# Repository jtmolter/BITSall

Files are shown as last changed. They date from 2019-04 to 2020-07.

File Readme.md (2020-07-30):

# Balloon Iridium Telemetry System

## DEPRECATED
Now part of https://github.com/UMDBPP/command_module

## Overview
This payload functions with an Iridium 9603 on a RockBlock carrier board. BITS has flown in various forms starting with NS-75 and continuously since NS-79 (10+ at this point) Iridium communications provide tracking from launch to landing, allowing for retrival of exact coordinates when landing in an area with no cell coverage. Additionally, the payload has been used as a long range link to then send data via XBee to other payloads.

Documentation is currently WIP (but for real this time)

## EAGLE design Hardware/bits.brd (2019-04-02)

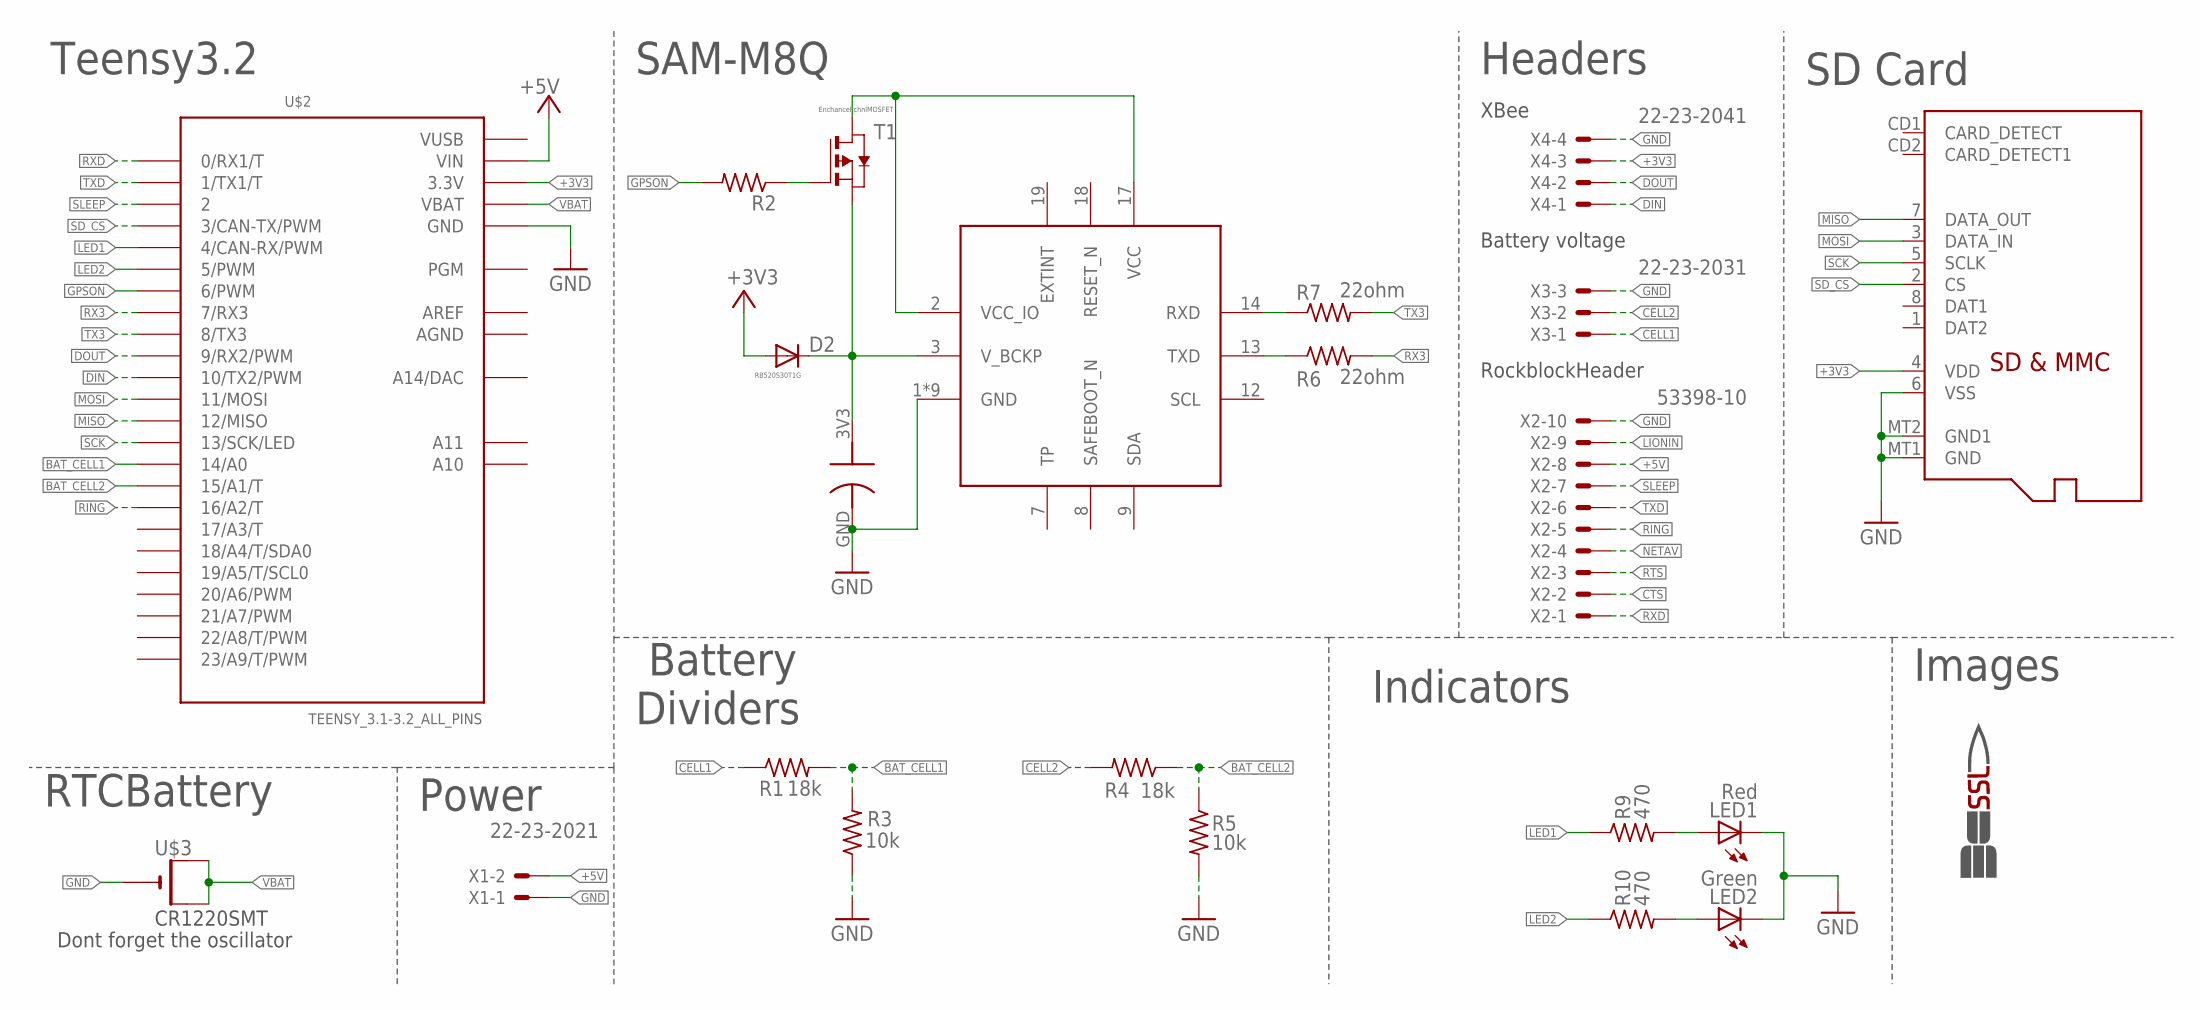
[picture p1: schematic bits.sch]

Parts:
C1: 0.2F elna supercap; ELNASUPERCAP
D2: RB520S30T1G; SOD523
IC1: SAM-M8Q
IMAG1: SSL.3IN_SILK; SSL_SILK_.3IN
LED1: Red; CHIP-LED0603
LED2: Green; CHIP-LED0603
R1, R4: 18k; R0603
R2: R-US_R0603; R0603
R3, R5: 10k; R0603
R6, R7: 22ohm; R0603
R9, R10: 470; R0603
T1: EnchancePchnlMOSFET; SOT-23
U$1: MICROSD
U$2: TEENSY_3.1-3.2_ALL_PINS; TEENSY_3.0-3.2&LC_ALL_PINS
U$3: CR1220SMT; CR1220-SMD
X1: 22-23-2021
X2: 53398-10
X3: 22-23-2031
X4: 22-23-2041

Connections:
+3V3: D2.A, U$1.4 (VDD), U$2.3.3V, U$2.3.3V1 (3.3V), X4.3
+5V: U$2.VIN, X1.2, X2.8
AGND: U$2.AGND
AREF: U$2.AREF
BAT_CELL1: R1.2, R3.2, U$2.14/A0
BAT_CELL2: R4.1, R5.1, U$2.15/A1 (15/A1/T)
CELL1: R1.1, X3.1
CELL2: R4.2, X3.2
CTS: X2.2
DIN: U$2.10 (10/TX2/PWM), X4.1
DOUT: U$2.9 (9/RX2/PWM), X4.2
GND: C1.GND, IC1.1 (GND), IC1.4 (GND), IC1.5 (GND), IC1.6 (GND), IC1.10 (GND), IC1.11 (GND), IC1.15 (GND), IC1.16 (GND), IC1.20 (GND), LED1.C, LED2.C, R3.1, R5.2, U$1.6 (VSS), U$1.MT1 (GND), U$1.MT2 (GND1), U$2.GND, U$2.GND1 (GND), U$3.-, X1.1, X2.10, X3.3, X4.4
GPS3V3: C1.3V3, D2.C, IC1.3 (V_BCKP), T1.2 (S)
GPSON: R2.2, U$2.6 (6/PWM)
LED1: R9.1, U$2.4 (4/CAN-RX/PWM)
LED2: R10.1, U$2.5 (5/PWM)
LIONIN: X2.9
MISO: U$1.7 (DATA_OUT), U$2.12 (12/MISO)
MOSI: U$1.3 (DATA_IN), U$2.11 (11/MOSI)
unnamed: R2.1, T1.3 (G)
unnamed: LED2.A, R10.2
unnamed: LED1.A, R9.2
unnamed: IC1.14 (RXD), R7.1
unnamed: IC1.13 (TXD), R6.1
unnamed: IC1.2 (VCC_IO), IC1.17 (VCC), T1.1 (D)
NETAV: X2.4
RING: U$2.16/A2 (16/A2/T), X2.5
RTS: X2.3
RX3: R6.2, U$2.7 (7/RX3)
RXD: U$2.0 (0/RX1/T), X2.1
SCK: U$1.5 (SCLK), U$2.13 (13/SCK/LED)
SD_CS: U$1.2 (CS), U$2.3 (3/CAN-TX/PWM)
SLEEP: U$2.2, X2.7
TX3: R7.2, U$2.8 (8/TX3)
TXD: U$2.1 (1/TX1/T), X2.6
VBAT: U$2.VBAT, U$3.+$1 (+), U$3.+$2 (+1)
VUSB: U$2.VUSB

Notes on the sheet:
SAM-M8Q
Teensy3.2
Headers
SD Card
RTCBattery
Dont forget the oscillator
RockblockHeader
Battery Dividers
Indicators
Power
Battery voltage
XBee
Images

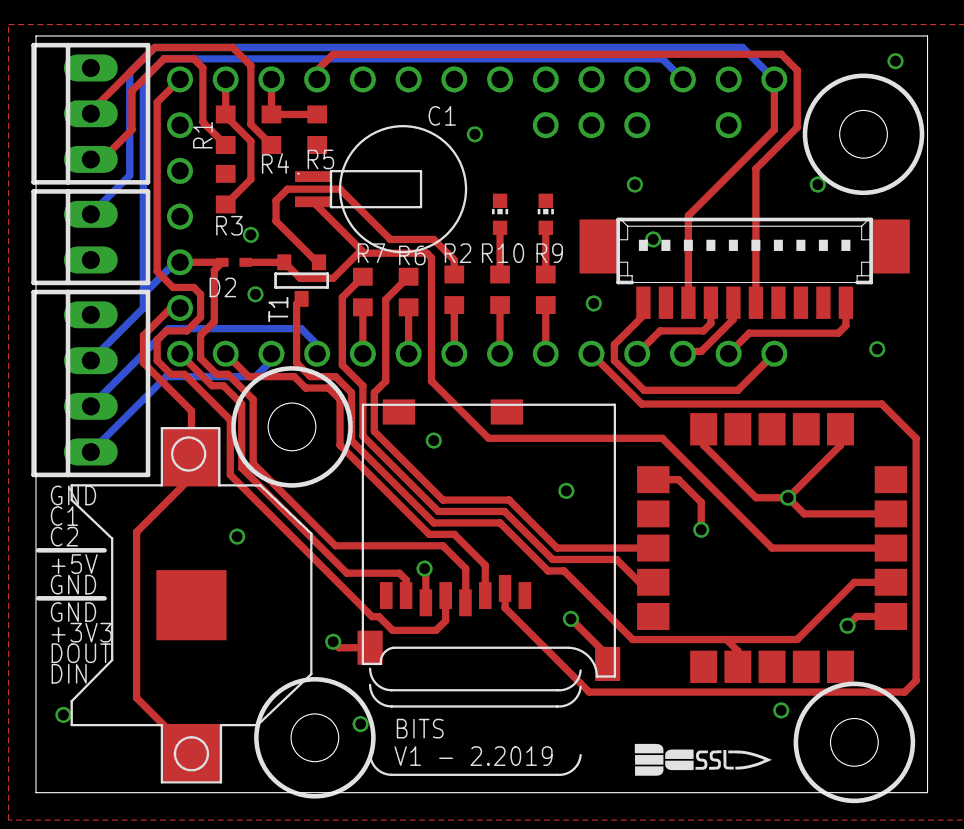
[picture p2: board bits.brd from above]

Board: 2 copper layers, 49.5 x 42.0 mm, 23 parts (1 on the bottom side), 30 nets.

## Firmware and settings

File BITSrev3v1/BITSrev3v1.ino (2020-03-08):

//UMD Nearspace Iridium Tracking Payload (BITS) {Balloon Iridium Tracking System)
//Written by Jonathan Molter and Luke Renegar
//Uses an Iridium 9603 SBD Modem for effective unlimited range, without the need for our own RF blackmagics*
//This software is specifically written with the bits3 board revisision

#include <XBee.h> //If using 900HP's this must be the custom cpp (or really any post gen2 XBees)
#include <IridiumSBD.h>
#include <SD.h>
#include <TinyGPS.h>

//Serial Ports (sketch requires 4 {Wellll technically 3 + DEBUG})
#define OutputSerial Serial     //USB debug
#define IridiumSerial Serial1   //Iridium 9603
#define XBeeSerial Serial2      //XBee
#define gpsserial Serial3       //GPS
//Pins
#define SLEEP_PIN_NO 5    // Iridium Sleep Pin
#define RING_PIN_NO 23    // Iridium Ring Alert Pin
#define chipSelect 6      // Pin for SPI
#define greenLED 2        // Green Status LED
#define redLED 3          // Red Status LED
#define GPS_ON 4

#define DIAGNOSTICS false // Change this to see diagnostics
#define XBEE_DEBUG true
const bool USEGPS = true; // Should be true 99% of the time
bool sendingMessages = true; // Whether or not the device is sending messages; begins as true TODO

//Setting default datarates
#define GPS_BAUD 9600
#define SBD_BAUD 19200

//XBee Addresses
const uint32_t BitsSL = 0x417B4A3B;   //BITS (white)Specific to the XBee on Bits (the Serial Low address value)
const uint32_t GroundSL = 0x417B4A36; //GroundStations (u.fl)
const uint32_t BlueSL = 0x417B4A3A;   //Blue (Blue Tape)
const uint32_t WireSL = 0x419091AC;   //Wire (wire antenna)
const uint32_t UniSH = 0x0013A200;    //Common across any and all XBees

//XBee object / global variables
XBee xbee = XBee();
XBeeResponse response = XBeeResponse();
ZBTxStatusResponse txStatus = ZBTxStatusResponse();
ZBRxResponse rx = ZBRxResponse();
ModemStatusResponse msr = ModemStatusResponse();
const int xbeeRecBufSize = 49; //Rec must be ~15bytes larger than send
const int xbeeSendBufSize = 34;
uint8_t xbeeRecBuf[xbeeRecBufSize];
uint8_t xbeeSendBuf[xbeeSendBufSize];

//GPS data struct and object
struct GPSdata{
  float GPSLat=-1;
  float GPSLon=-1;
  unsigned long GPSTime=-1;
  long GPSAlt=-1;
  int GPSSats=-1;
};
TinyGPS gps;
GPSdata gpsInfo;

//Interval definitions
const long signalCheckInterval = 15000;
unsigned long messageTimeInterval = 60000; // In milliseconds; 300000 is 5 minutes; defines how frequently the program sends messages, now changeable                                                                      
const long shutdownTimeInterval = 14400000; // In milliseconds; 14400000 is 4 hours; defines after what period of time the program stops sending messages

//Initializing Log Files; Must be in form XXXXXXXX.log; no more than 8 'X' characters
File gpsLogFile;
File rxLogFile;
File txLogFile;

const String gpsLogName =   "GPS.LOG";  //1 sec position/altitude updates
const String eventLogName = "EVENT.LOG";//Events Iridium/XBee (Special one thanks to Luke)
const String rxLogName =    "RX.LOG";   //Iridium Uplinks   (toBalloon)
const String txLogName =    "TX.LOG";   //Iridium Downlinks (toGround)



// Program Timing
unsigned long startTime;
unsigned long lastMillisOfMessage = 0;
unsigned long lastSignalCheck = 0;
unsigned long lastLog = 0;

// Iridium Global Buffers
//#define SBD_RX_BUFFER_SIZE 100 // Max size of an SBD message TODO(1) DELETE
#define maxPacketSize 128		//Standard(GPS/TIME, etc.) + Message Data
#define downlinkMessageSize 100 //Message Data
#define RX_BUF_LENGTH 49		//Uplink Buffer Size

uint8_t rxBuf[RX_BUF_LENGTH]; 			   //Uplink Buffer
//uint8_t sbd_rx_buf[SBD_RX_BUFFER_SIZE];  //TODO(1) DELETE ?(what is this even doing...)
char downlinkMessage2[downlinkMessageSize];//Downlink Buffer
bool downlinkData;

int sbd_csq; //Signal Qual

// The best global
int arm_status = 42;//armed when = 42

// Declare the IridiumSBD object
IridiumSBD modem(IridiumSerial);

//Possible Iridium Error Codes
#define ISBD_SUCCESS             0
#define ISBD_ALREADY_AWAKE       1
#define ISBD_SERIAL_FAILURE      2
#define ISBD_PROTOCOL_ERROR      3
#define ISBD_CANCELLED           4
#define ISBD_NO_MODEM_DETECTED   5
#define ISBD_SBDIX_FATAL_ERROR   6
#define ISBD_SENDRECEIVE_TIMEOUT 7
#define ISBD_RX_OVERFLOW         8
#define ISBD_REENTRANT           9
#define ISBD_IS_ASLEEP           10
#define ISBD_NO_SLEEP_PIN        11
#define SBD

void setup()
{
  Serial.begin(9600);
  delay(5);
  Serial.println("BITSrev3v1");
  gpsserial.begin(9600);
  GPSINIT(); //Setup the GPS
  gpsserial.end();
  gpsserial.begin(GPS_BAUD);
  IridiumSerial.begin(SBD_BAUD);
  Serial2.begin(9600);
  xbee.setSerial(Serial2);
  startBlinks();

//Open Files
  SD.begin(chipSelect);
  gpsLogFile = SD.open(gpsLogName, FILE_WRITE);
  rxLogFile = SD.open(rxLogName, FILE_WRITE);
  txLogFile = SD.open(txLogName, FILE_WRITE);
  delay(10);
  gpsLogFile.println("INIT_GPS_LOG");
  rxLogFile.println("INIT_RX_LOG");
  txLogFile.println("INIT_TX_LOG");
  gpsLogFile.flush();
  rxLogFile.flush();
  txLogFile.flush();
  Serial.println("MadeLogs");
  logprintln("INIT_LOG_LOG");

  //memset(sbd_rx_buf, 0, SBD_RX_BUFFER_SIZE); //TODO(1) DELETE ?

  //XBee Init Message to ground stations
  String("Init").getBytes(xbeeSendBuf,xbeeSendBufSize);   //Convert "Init" 2 bytes, dump into Message buffer
  xbeeSend(GroundSL,xbeeSendBuf);                         //(Target,Message)
  
int err;
#ifdef SBD  // Begin satellite modem operation
  OutputSerial.println("Starting modem...");
  err = modem.begin();
  modem.useMSSTMWorkaround(false);//SUPER NF TESTTHIS TODO(2)
  modem.adjustSendReceiveTimeout(120);
  if (err != ISBD_SUCCESS)
  {
    OutputSerial.print("Begin failed: error ");
    OutputSerial.println(err);
    logprint("Begin failed: error ");
    logprintln(err);
    if ((err == ISBD_NO_MODEM_DETECTED) || (err == 5))
      Serial.println("No modem detected: check wiring.");
    return;
  }
  OutputSerial.println("Modem started");

  #ifdef ISBD_CHECK_FIRMWARE // Example: Print the firmware revision
    char version[12];
    err = modem.getFirmwareVersion(version, sizeof(version));
    if (err != ISBD_SUCCESS)
    {
      OutputSerial.print("FirmwareVersion failed: error ");
      OutputSerial.println(err);
      logprint("FirmwareVersion failed: error ");
      logprintln(err);
      return;
    }
    OutputSerial.print("Firmware Version is ");
    OutputSerial.println(version);
  #endif

  // From 0-5, 2 or better is preferred (Still works at 0)
  err = modem.getSignalQuality(sbd_csq);
  if (err != ISBD_SUCCESS)
  {
    OutputSerial.print("SignalQuality failed: error ");
    OutputSerial.println(err);
    logprint("SignalQuality failed: error ");
    logprintln(err);
    sbd_csq = -1;
    return;
  }

  OutputSerial.print("From 0 to 5, signal qual is: ");
  OutputSerial.println(sbd_csq);
#endif

String gpsPacket;

if(USEGPS){
  OutputSerial.println("TryingGPS");

  //GPS LOCK INIT
    while((gpsInfo.GPSAlt<=0)||(gpsInfo.GPSAlt>100000)) //Outside of a reasonable range
    {
      //delay(500);
      //output();
      while (gpsserial.available()){
          if (gps.encode(gpsserial.read())){
          gpsInfo = getGPS();
        break;
        }
      }
    }
    
    gpsPacket = String(gpsInfo.GPSTime)+","+String(gpsInfo.GPSLat,4)+","+String(gpsInfo.GPSLon,4)+","+String(gpsInfo.GPSAlt);
    txLogFile.println(gpsPacket);
    logprintln("GotLock");
    gpsLockBlink();
    OutputSerial.println("gpsPacket  " +String(gpsPacket));
}else{
  OutputSerial.println("Not Using GPS");
  gpsPacket = "test";
}


//Honestly consider canning this whole section, really not needed considering loop does the same thing
#ifdef SBD
// Send the message
  char sbd_buf[49];//TX BUFFER
  OutputSerial.print("Trying to send the message.  This might take several minutes.\r\n");
  gpsPacket.toCharArray(sbd_buf,49);
  err = modem.sendSBDText(sbd_buf);//Sends an initial packet AFTER gps has locked.
  if (err != ISBD_SUCCESS)
  {
    OutputSerial.println("sendSBDText failed: error "+String(err));
    OutputSerial.println();
    logprint("sendSBDText failed: error ");
    logprintln(err);
    if (err == ISBD_SENDRECEIVE_TIMEOUT)
      OutputSerial.println("Try again with a better view of the sky.");
      logprintln("Try again with a better view of the sky.");
  }else{
    OutputSerial.println("Success, sent = "+String(sbd_buf));
    logprintln("Success, sent = "+String(sbd_buf));
  }
#endif

        String("EnteringLoop").getBytes(xbeeSendBuf,xbeeSendBufSize);
        xbeeSend(GroundSL,xbeeSendBuf);
}

void loop()
{  
  ISBDCallback(); //During the Iridium retry protocol anything that still needs to happen needs to go in here

  xbeeRead();
  LogPacket();
  
//Check Signal Quality
  if (((millis() - lastSignalCheck) > signalCheckInterval) && (millis() < shutdownTimeInterval)) {
    int new_csq = 0;
    int csq_err = modem.getSignalQuality(new_csq);
    if(csq_err == 0) // if executed during an Iridium session, this will yield an ISBD_REENTRANT; keep previous value
    {
      sbd_csq = new_csq;
    }
    else if(csq_err == ISBD_REENTRANT){
      //KeepCalm, carry on  
    }else{
      logprint("CSQ error code = ");
      logprintln(csq_err);
    }
    lastSignalCheck = millis();
  }

//Transmit Via Iridium
  // If not currently transmitting, and at time, and transmitting messages ON, transmit
  if ((sbd_csq > 0 && (millis() - lastMillisOfMessage) > messageTimeInterval) && (millis() < shutdownTimeInterval) && sendingMessages) {

    size_t rx_buf_size = RX_BUF_LENGTH; //RECENT CHANGE via TODO(1)

  //Assesmble the packet to be sent to the ground
    char Packet2[maxPacketSize];
    snprintf(Packet2,maxPacketSize,"%06d,%4.4f,%4.4f,%u",gpsInfo.GPSTime,gpsInfo.GPSLat,gpsInfo.GPSLon,gpsInfo.GPSAlt); //Build the packet

  //If there is stuff to downlink than do
    if(downlinkData){ 
      logprint("DownAttempt: ");
      logprintln(downlinkMessage2);
      strncat(Packet2,downlinkMessage2,(maxPacketSize - strlen(Packet2) - 1));  //Add data from downlinkMessage2 into Packet2, check for size
      downlinkData = false;
      memset(downlinkMessage2, 0, downlinkMessageSize);                         //Clear downlink message
    }    
    
    logprint(Packet2);logprintln("Loop Sending");
    OutputSerial.println("Loop Sending");
    txLogFile.println(Packet2);
    txLogFile.flush();

  //SEND/RECEIVE DATA, return status
    uint8_t sbd_err = modem.sendReceiveSBDText(Packet2,rxBuf,rx_buf_size);  //Message, RecieveBuffer, SizeOfBuffer

    logprint("SBD send receive completed with return code: ");
    logprintln(sbd_err); // 0 is good
    OutputSerial.println("Send Error:  " +String(sbd_err));

    rxLogFile.print(String(gpsInfo.GPSTime)); //Log time of RX
    rxLogFile.print("\t");
    
  //Process Received Messages
    uplink(); //Run uplink message handling (bitsIncoming)
 
    for (int k = 0; k < rx_buf_size; k++)//Prints RX characters to SD file
    {
      rxLogFile.write(rxBuf[k]); //Trying write instead of print, shoud fix garbage data
      rxBuf[k] = 0;
      delay(1);
    }
    rxLogFile.println();
    rxLogFile.flush();

    lastMillisOfMessage = millis();
  }
}//End of Loop


bool ISBDCallback() //Functions that occurs during packet transmit sequence delay
{
  //Parse the GPS without delay
  while (gpsserial.available()){
    if (gps.encode(gpsserial.read())){
      gpsInfo = getGPS();
      break;
    }
  }

  //Check the Xbee
  xbeeRead();
  
  LogPacket();
  
  return true;
}

static void logprint(String s)
{
  File dataFile = SD.open(eventLogName, FILE_WRITE);
  dataFile.print(s);
  dataFile.close();
}

static void logprint(int i)
{
  File dataFile = SD.open(eventLogName, FILE_WRITE);
  dataFile.print(i);
  dataFile.close();
}

static void logprint(double d)
{
  File dataFile = SD.open(eventLogName, FILE_WRITE);
  dataFile.print(d);
  dataFile.close();
}

static void logprintln(String s)
{
  File dataFile = SD.open(eventLogName, FILE_WRITE);
  dataFile.println(s);
  dataFile.close();
}

static void logprintln(int i)
{
  File dataFile = SD.open(eventLogName, FILE_WRITE);
  dataFile.println(i);
  dataFile.close();
}

static void logprintln(double d)
{
  File dataFile = SD.open(eventLogName, FILE_WRITE);
  dataFile.println(d);
  dataFile.close();
}

static void logprintln32(uint32_t d)
{
  File dataFile = SD.open(eventLogName, FILE_WRITE);
  dataFile.println(d,HEX);
  dataFile.close();
}

#if DIAGNOSTICS
void ISBDConsoleCallback(IridiumSBD *device, char c)
{
  OutputSerial.write(c);
}

void ISBDDiagsCallback(IridiumSBD *device, char c)
{
  OutputSerial.write(c);
}
#endif

void LogPacket(){
  if(millis()-lastLog>1000){
    char gpsLogPacket2[35];
    
    char exactTime[9];//A somewhat convaluted way of adding : into the integer timestamp... //TEST
    snprintf(exactTime,7,"%d",gpsInfo.GPSTime);
    char hour[3];char min[3];char sec[3];
    strncpy(hour, &exactTime[0], 2);hour[2] = '\0';
    strncpy(min, &exactTime[2], 2);min[2] = '\0';
    strncpy(sec, &exactTime[4], 2);sec[2] = '\0';
    snprintf(exactTime,9,"%s:%s:%s",hour,min,sec);
    
    snprintf(gpsLogPacket2,35,"%s,%4.4f,%4.4f,%u",exactTime,gpsInfo.GPSLat,gpsInfo.GPSLon,gpsInfo.GPSAlt); //Fix Timestep
    gpsLogFile.println(gpsLogPacket2);
    
    gpsLogFile.flush();
    lastLog=millis();
  }
}

//* This version actually hopes to leverage the power of proper link budget calculations to obtain XBee to ground comms
//  without the need for Iridium

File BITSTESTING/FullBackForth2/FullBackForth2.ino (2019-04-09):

#include <XBee.h>
#include <SoftwareSerial.h>

XBee xbee = XBee();
XBeeResponse response = XBeeResponse();
//SoftwareSerial xbeeSerial(2, 3);
#define xbeeSerial Serial2


const uint32_t BitsSL = 0x417B4A3B;
const uint32_t MarsSL = 0x417B4A3A;
const uint32_t GroundSL = 0x417B4A36;
const uint32_t UniSH = 0x0013A200;

ZBTxStatusResponse txStatus = ZBTxStatusResponse();
ZBRxResponse rx = ZBRxResponse();
ModemStatusResponse msr = ModemStatusResponse();
const int xbeeRecBufSize = 50; //Rec must be ~15bytes larger than send
const int xbeeSendBufSize = 35;
uint8_t xbeeRecBuf[xbeeRecBufSize];
uint8_t xbeeSendBuf[xbeeSendBufSize];


void setup() {
  Serial.begin(9600);
  xbeeSerial.begin(9600);
  delay(500);
  xbee.setSerial(xbeeSerial);
  Serial.println("Startup");
}

void loop() {
  if(Serial.available()>0){
    Serial.println("Sending");
    Serial.readBytes((char*)xbeeSendBuf,xbeeSendBufSize);
    xbeeSend(GroundSL,xbeeSendBuf);
  }
  
  xbeeRead();
}

bool xbeeSend(uint32_t TargetSL,uint8_t* payload){
  XBeeAddress64 TargetAddress = XBeeAddress64(UniSH,TargetSL);
  ZBTxRequest zbTx = ZBTxRequest(TargetAddress, payload, xbeeSendBufSize); //Assembles Packe
  xbee.send(zbTx);              //Sends packet
  memset(xbeeSendBuf, 0, xbeeSendBufSize);
  if (xbee.readPacket(500)) {                                       //Checks Reception
    if (xbee.getResponse().getApiId() == ZB_TX_STATUS_RESPONSE) {
      xbee.getResponse().getZBTxStatusResponse(txStatus);
      if (txStatus.getDeliveryStatus() == SUCCESS) {
        Serial.println("SuccessfulTransmit");
        return true;
      } else {
        Serial.println("TxFail");
        return false;
      }
    }
  } else if (xbee.getResponse().isError()) {
    Serial.print("Error reading packet.  Error code: ");
    Serial.println(xbee.getResponse().getErrorCode());
  }
  return false;
}

void xbeeRead(){
  xbee.readPacket(); //read buffer
    if (xbee.getResponse().isAvailable()) { //got something
      if (xbee.getResponse().getApiId() == ZB_RX_RESPONSE) { //got a TxRequestPacket
        xbee.getResponse().getZBRxResponse(rx);
        
        uint32_t incominglsb = rx.getRemoteAddress64().getLsb();
        Serial.print("Incoming Packet From: ");
        Serial.println(incominglsb,HEX);
        if(rx.getPacketLength()>=xbeeRecBufSize){
          Serial.print("Oversized Message: ");
          Serial.println(rx.getPacketLength());
        }
        memset(xbeeRecBuf, 0, xbeeRecBufSize); // Clears old buffer
        memcpy(xbeeRecBuf,rx.getData(),rx.getPacketLength());
        if(incominglsb == BitsSL){
          processBitsMessage();
        }
        if(incominglsb == MarsSL){
          processMarsMessage();
        }
        if(incominglsb == GroundSL){
          processGroundMessage();
        }    
      }
    } //else if (xbee.getResponse().isError()) {
      //Serial.print("error code:");
      //Serial.println(xbee.getResponse().getErrorCode());
    //}
}

void processBitsMessage(){
  Serial.println("RecFromBits");  
}
void processGroundMessage(){
  Serial.print("RecFromGND: ");
  Serial.write(xbeeRecBuf,xbeeRecBufSize);
  
  if(strstr((char*)xbeeRecBuf,"test")){ //Checks if "test" is within buffer
      Serial.println("");
      Serial.println("ackTest");
      String("PacketAck").getBytes(xbeeSendBuf,xbeeSendBufSize);
      xbeeSend(GroundSL,xbeeSendBuf);
  }
  if(strstr((char*)xbeeRecBuf,"TG")){ //Checks if "test" is within buffer
      Serial.println("");
      Serial.println("ToGround");
      String("ToGNDAck").getBytes(xbeeSendBuf,xbeeSendBufSize);
      xbeeSend(GroundSL,xbeeSendBuf);
  }  
}
void processMarsMessage(){
  Serial.println("RecFromGND");  
}

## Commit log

2019-04-02 First push of full v1 code
    [bits.brd, bits.sch]
2019-04-16 Updating code post launch
    [bits2.brd, bits2.sch]
2019-04-26 Post flight crash prevention
    [BITS2019v2.ino, BITSGroundStation.ino, XBeeMethods.ino]
2019-06-30 Fix CS, timestamp problem resolve, echo on cmd rec
    [XBeeMethods.ino, bitsStatusIndicators.ino]
2019-07-23 NS-86 mods and more fix attempts
    [BITS2019v2.ino, BITSGroundStation.ino, XBeeMethods.ino]
2019-10-09 File Sorting
    [bits.brd, bits.sch, bits2.brd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]
2020-01-06 Flipped the GPS mosfet around
    [bits2.sch]
2020-01-06 Added value for gps Mosfet
    [bits2.sch]
2020-03-08 Created new directory for rev3 boards
2020-03-08 Preparing software for Boardrev3, documenting
